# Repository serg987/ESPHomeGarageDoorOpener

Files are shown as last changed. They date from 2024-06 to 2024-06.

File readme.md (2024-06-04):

# ESPHome Garage Door Opener Controller for Devices with Optical Encoder

## Description

This is a small [ESPHome](https://esphome.io/) project designed to control and monitor a garage 
door opener using an optical encoder as a movement sensor. For example, the Precision PDS-800. 
Key features include:

- Fits entirely within the opener case, with no external wiring except for a LAN 
cable if LAN communication is used.
- No additional sensors are required to monitor door state/position.
- No relays or other switching devices are needed.
- In its minimal configuration, it requires only 2 input and 1 output pins.
- Additional ESPHome sensors can be added.
- Displays not only open/closed positions but also opening/closing movements. 
It can detect mechanical failures and when the door has been open for an extended period.
- Includes a simple Lovelace UI card for Home Assistant.

However, there are some drawbacks:

- The door state cannot be recognized until the first movement occurs.
- Modifying the opener voids its warranty.
- It requires initial setup and does not work out of the box.
- A hardware pulse counter pin is required, making it incompatible with the ESP8266.

## Warning

This project has at least medium complexity. You must have previous experience with ESPHome, 
moderate electrical knowledge, and soldering skills. You should be capable of working safely 
with circuits that may have high (>100V) voltage. There is a risk of electric hazard. 
All connections must be made while the device is fully unplugged from the power outlet.

Implementing these changes will void the warranty of the garage door opener and possibly 
the entire garage door setup. You may damage the door opener and/or the garage door setup. 
This manual may not cover all aspects, so you should apply your own knowledge and risk 
analysis if something is unclear. The software and manual are provided "as is," 
and by proceeding, you agree to take responsibility for any damage or losses—physical, 
monetary, mental, or otherwise—that may occur. The author does not hold any liability 
for any such consequences.

## How it works ##

There are some challenges while working with optical encoder in ESPHome. ESPHome does have
[rotary encoder](https://esphome.io/components/sensor/rotary_encoder) sensor, but in this
case pulses have a period of around 40ms and seems ESPHome misses some and sometimes even 
reports opposite direction during rotation if we are using just this rotary encoder 
component.

Optical sensor has a resolution of about 1 cm, so in a case of a door coming to an end position
the belt tries to drop the tension and may produce a few pulses. We need to ignore them.

After the power up the garage door has 'Unavailable' state. Once optical encoder starts to 
rotate, after first 5 pulses we decide if it is opening or closing. Then we do not care about
encoder and just count pulses on a hardware counter. We wait till pulses stop coming and if 
the number of pulses is enough to consider the door fully opened or closed we set its state,
otherwise it is a failure. If we receive only one pulse within certain period (250ms) we 
ignore it - it is just a parking.

If the door is opened for 30 mins the state is changed to 'Opened timeout'. It can be used
in some automation scripts.

The device exposes: 

- two 'hardware' buttons that connected directly to 'button' 
connector of the opener (one for the door and one for the light). Door button is not exposed
by default (see below). Light button is optional, you can remove it and not install
components for it
- two 'software' buttons for opening and closing the door. Better to use these ones
in any automation as they check the current state of the door before making an action
- `select` input for the door state
- minimum counter value - for initial set up (see below)
- optional - temperature, humidity and atmospheric pressure sensors on AHT20/BMP280 board

You can add other sensors as well, both hardware and software.

## Schematics ##

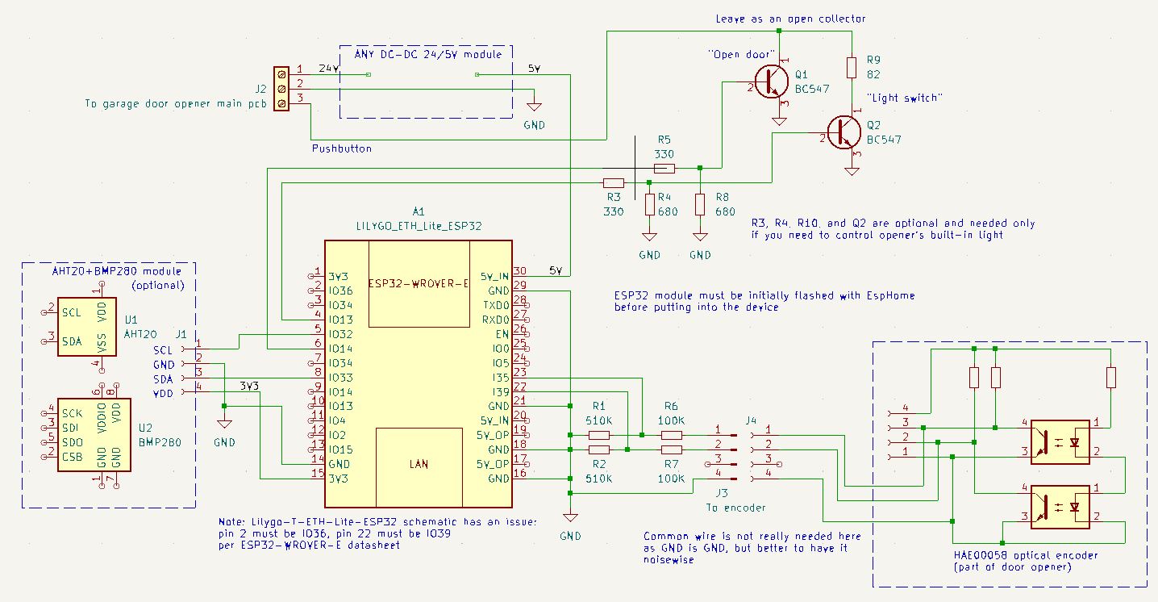
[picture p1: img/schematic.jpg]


Pretty simple. DC/DC converter of 24V/5V, ESP32 module, a few discrete components.

AHT20+BMP280 module is optional, as well as the circuit for light switch.

Author's device is based on LILYGO T-ETH-Lite module as LAN connection was needed, but in
general any ESP32 module can be used. Just define proper pins in the yml file. The mandatory
thing is to assign `encoder_pulse_counter` sensor (and one of the encoder inputs) to a hardware 
pulse counter pin. Usually it is marked as RTC in datasheets. In this device it is IO35 on 
the schematic diagram.

## Setting up ##

### Assembling ###

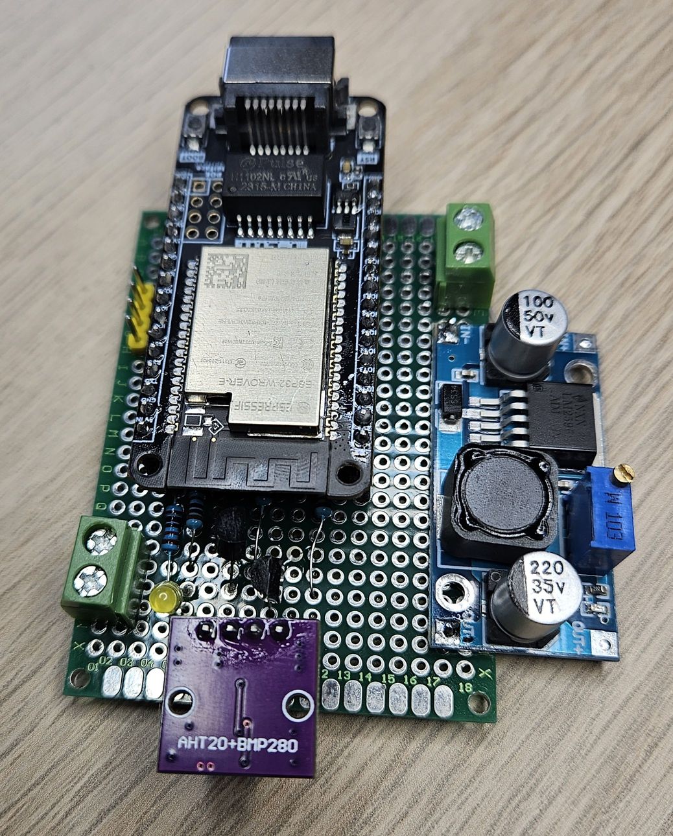
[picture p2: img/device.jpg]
device_photo


Note: This picture is only for a reference. This particular device has some debug components 
like LED and a few resistors. It has bad connectors as well (see below). You should follow 
the schematics, not this picture.

Components for light button and ambient sensor are optional and may be not installed. Just 
remove them from yml in this case as well.

The device was made on a prototype board and used mixed wired and SMD components. As there 
is no USB connector, the device must be initially flashed with ESPHome in any way and only 
then installed in the garage opener.

### Power ###

The door opener does have a 5V power source, but it is not clear how much load it can handle.
So for safety this device is powered from 24V source via DC-DC power module. Important! Before
connecting ESP32 module to power module check its output voltage. It must be 5V +/-10%.

### Fitting inside opener case ###

Wherever you find an empty space (there is plenty of it) and convenient for you to attach it.
For LAN connector a hole in the covering should be made. Author's installation looks like

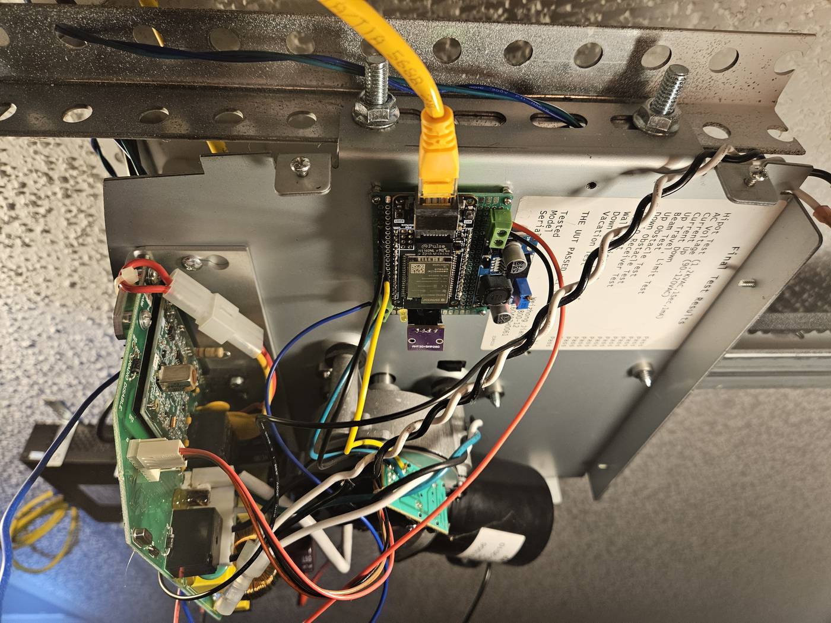
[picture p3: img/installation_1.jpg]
installation


and with the cover on:

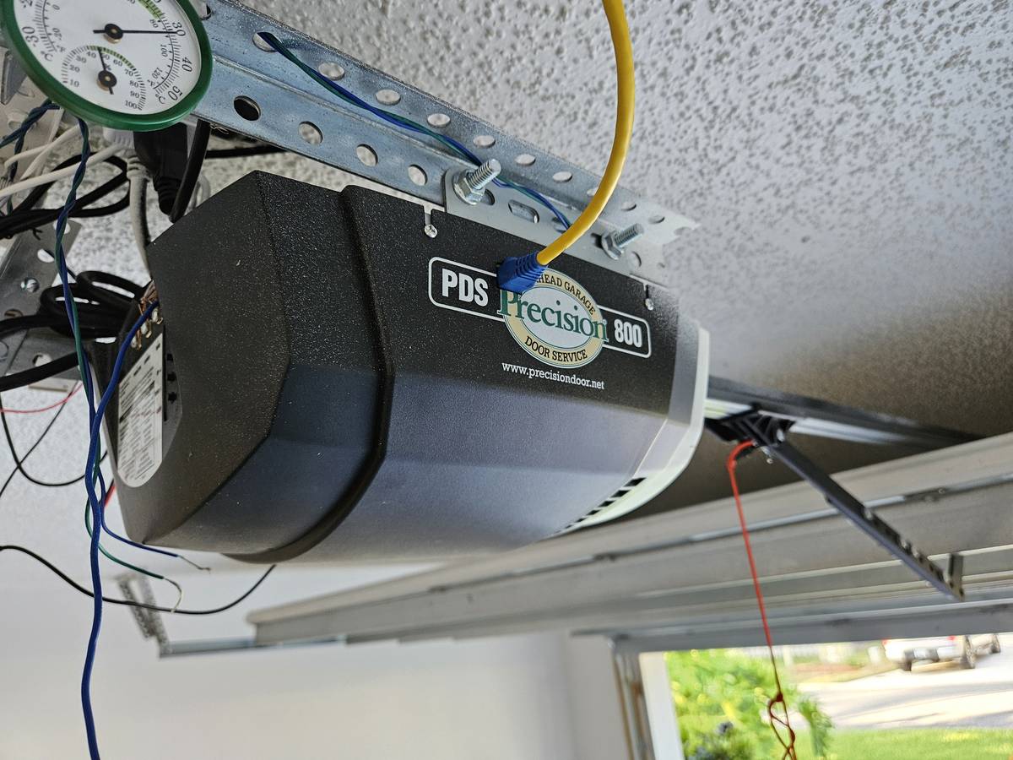
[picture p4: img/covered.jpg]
cover_on


### Connection to the opener circuits ###

Warning (one more time)! Internal circuits have high (>100V) voltage. There is a risk of 
electric hazard. All connections must be made while the opener is fully unplugged from the 
power outlet. The proposed changes will void garage door opener warranty and maybe in some
cases all the garage door set up. You may damage the door opener and/or garage door, as well
as ESP32 and/or other components. If you are not sure - ask someone who has an experience in 
this stuff.

Find 24V source. It is a big electrolytic capacitor in the middle of PCB, do not mess with 
another one on the left side (if look on the photo below) which is the high voltage one. In 
any case check the voltage on the capacitor before making a connection. It should be 24-27V 
in idle. Again, measure on a working opener with all the precautions, connect only on fully 
unplugged one. 

'Button' connection is pretty straightforward - just solder a wire to the PCB pad under it.

In Precision PDS-800 the connection points are:

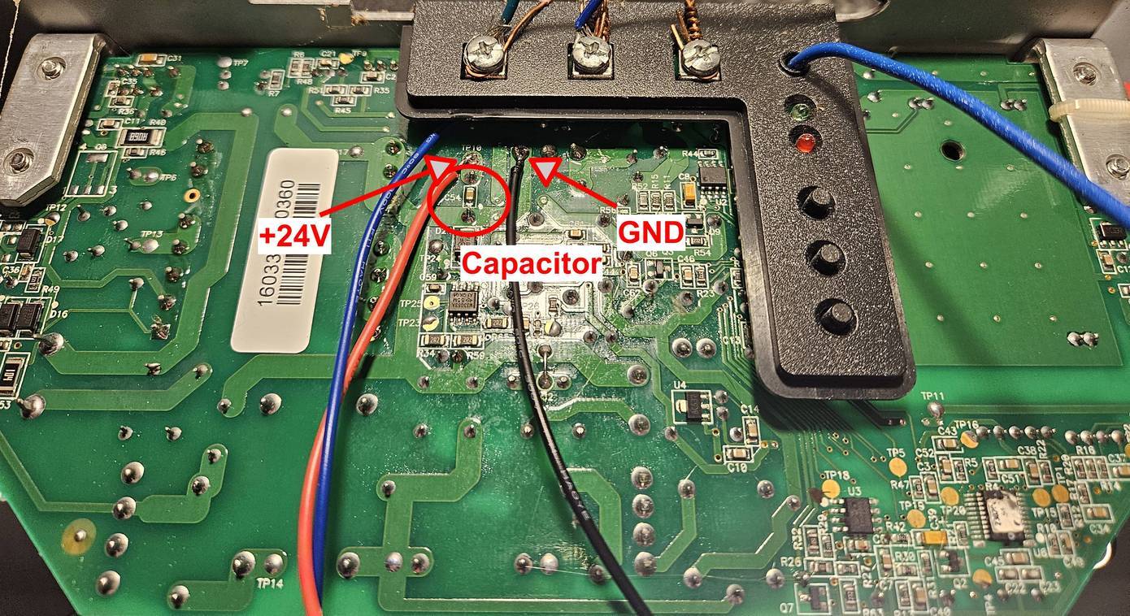
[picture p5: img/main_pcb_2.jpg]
main_pcb_connection_1


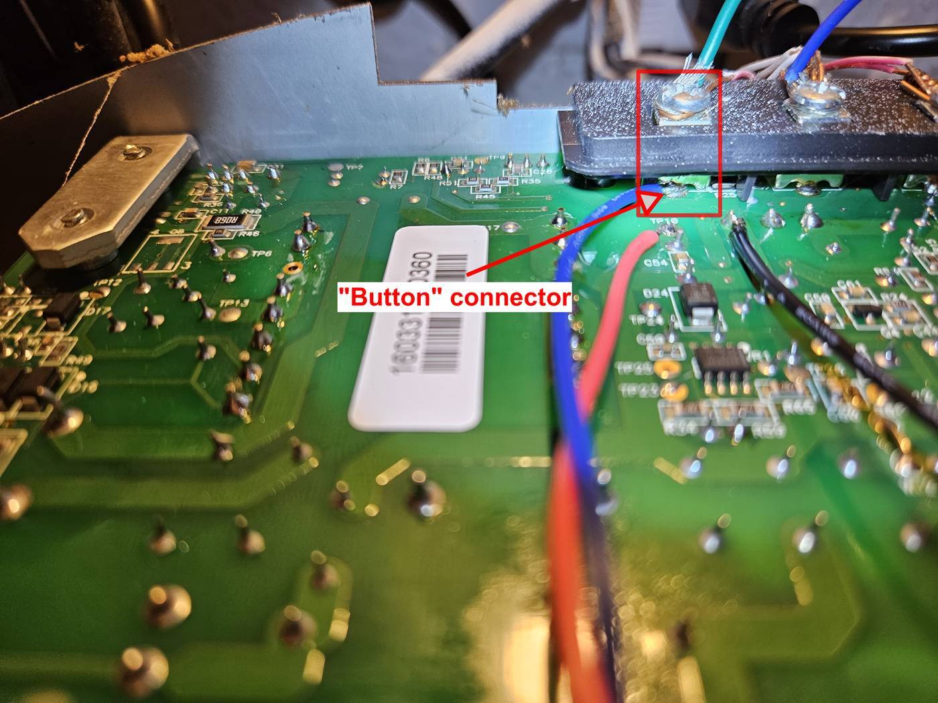
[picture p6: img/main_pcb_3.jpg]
main_pcb_connection_2


Locate signal wires on the optical encoder PCB.  

In Precision PDS-800 the connection points are:

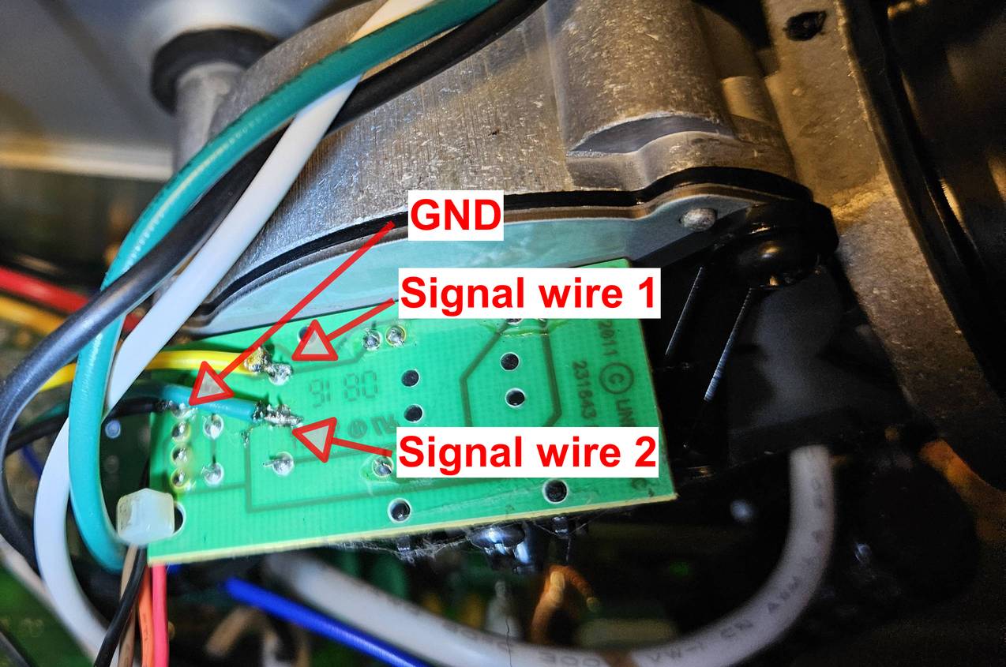
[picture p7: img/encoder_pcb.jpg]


Just connect them as they are, if the opening door will appear as closing in ESPHome, you
just swap those wires later.

Author's device uses screwed connectors - it is a **bad** solution. Use a connector that holds
wires in place and would not let them contact each other and other circuits. A molex connector
may be a good choice.

For other models of openers you would need (only brief instructions here, as you should 
know for sure what you are doing):
- check if bipolar transistor triggers button. Check the voltage on the button pin. Choose
the transistor accordingly
- find a power source. It may be or may be not 24V. Choose a proper DC-DC module capable
of handling input voltage
- check an amplitude and a period of pulses on the optical encoder
- measure internal resistance on the main board where optical encoder is connected.
- choose voltage divider based on the amplitude and resistance. Whole resistance of the 
divider must be at least 5 times more than the internal one. For example, in PDS-800 the 
resistance is pretty high - 100K. And the amplitude is 3.9V. So the divider is 
610K: 510K + 100K.
- based on the pulse period tweak timings in the yml file

### Debugging and Setting the Counter Value

After connecting the device to the opener, it should power up and display its UI. 
Press your opener button or click the `Garage door button` in the device UI. The door 
should start moving, and the device must recognize whether it is opening or closing. 
If it shows movement in the opposite direction, unplug the opener from the power socket
and swap the two signal wires to the optical sensor.

After the first movement, the state should change from unavailable to opened/closed, and 
encoder_debug_min_value should be updated. Note its value:

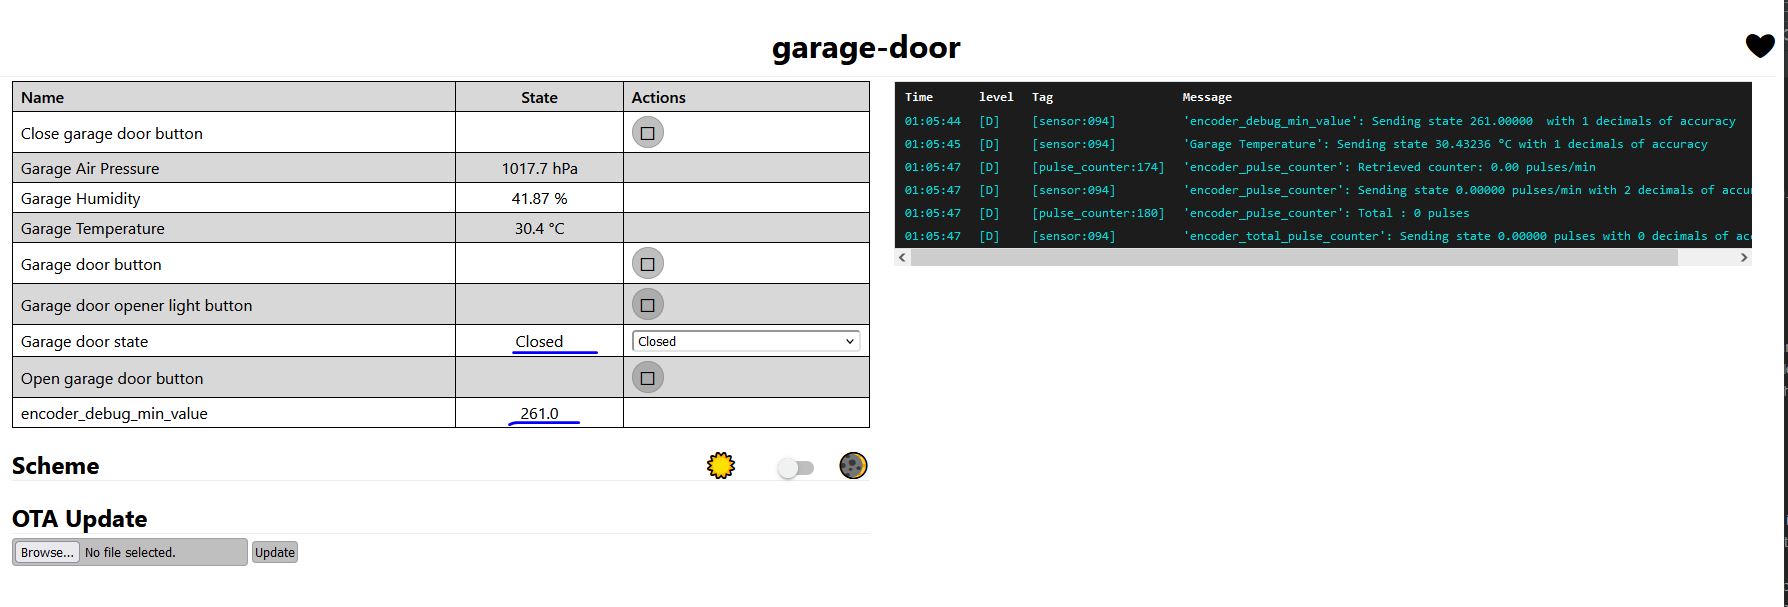
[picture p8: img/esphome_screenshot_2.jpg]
Esphome screenshot
 

Open/close the door again. The value may change slightly. Leave the device for a few days 
and monitor the value periodically. It should not change more than a few pulses overall. 
If it consistently decreases, there may be an error in the assembly or optical encoder 
connection (amplitude/pulse period). In such cases, an oscilloscope might be necessary for 
troubleshooting.

After a few days, if there are no significant changes, subtract 3 from the observed value for 
safety and set it in `encoder_full_way.initial_value`. You can then comment out everything 
related to `encoder_debug_min_value` as it is no longer needed. Recompile the project and flash 
the device again.

Now it is ready for use. Monitor it for a few more days—there should be no 'Failure' states, 
and it should display states correctly.

## Home Assistant Lovelace UI card ##

The [button-card](https://github.com/custom-cards/button-card) needs to be installed, 
which can be done via HACS, for example.

If this project is compiled as is, the card should work seamlessly. Otherwise, adjust the 
entities for both the select input and buttons according to their IDs in Home Assistant.

## Support

Support is not promised, but the author will try to resolve coming issues if time allows it. 
PRs are welcome.
